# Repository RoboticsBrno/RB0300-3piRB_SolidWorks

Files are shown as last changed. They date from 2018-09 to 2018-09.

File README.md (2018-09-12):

# SOČ 2016 - Nadstavbová deska pro robota Pololu 3pi
**Autor:** Petr Bobčík

Vítejte v příloze mé práce Nadstavbová deska pro robota Pololu 3pi

#### V této příloze naleznete: 
1) Dokumenty
1) Eagle
1) Obhajoba
1) Použité obrázky
1) SolidWorks

#### Podrobnější obsah jednotlivých složek:
1) Přehled projektu s grafm pro IR senzor, obrázek s konceptem zapojení a tabulku potřebných součástek na pájení.
2) Finální verze desky a schéma k ní v programu Eagle + schéma s deskou k nárazovému senzoru.
3) Text samotné sočky a prezentaci k ní.
4) Veškeré obrázky použity jak v prezentaci, tak v textové práci.
5) Kompletní 3D model robota Pololu 3pi s přídavným shieldem.

## Cíl práce
<p>Cílem této práce byl návrh nadstavbové desky (shieldu) pro robota Pololu 3pi. Konstrukce robota je od výrobce optimalizována
na soutěžní disciplínu „sledování čáry“, kde robot dosahuje výborných výsledků a nemá mezi komerčně dostupnými produkty konkurenci. Ovšem při složitější variantě této disciplíny “najdi čáru“, konající se na Robotickém dni v Praze, kde dráha obsahuje rozpojky, odbočky, nebo překážky, není možné s ním závodit. Můj shield může posloužit, kromě možné účasti na soutěžích, také ve výuce. V ní si student může
robota sám naprogramovat. Přidáním funkcí a senzorů bude robot univerzálnější než doposud.</p>

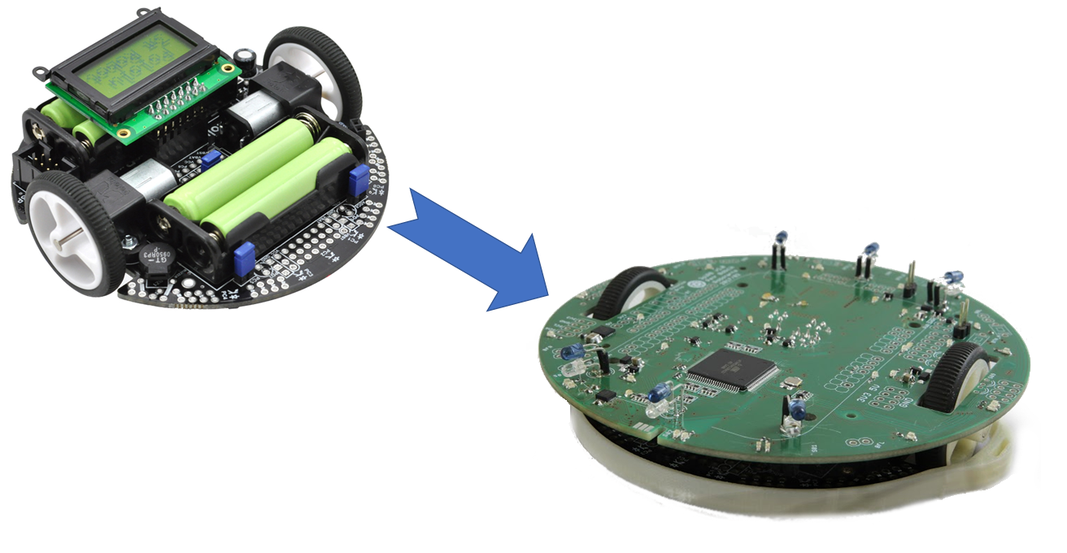
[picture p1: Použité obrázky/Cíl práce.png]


<p>Práce řeší rozšíření možností využití robota Pololu 3pi návrhem nadstavby s doplňkovými funkcemi.
Přidané funkce umožňují robotovi snímat podněty ze svého okolí. Další navrženou částí je nárazník pro ochranu před mechanickým poškozením, ke kterému v praxi velmi často dochází. Tyto nárazy způsobovli nefunkčnost senzorů odrazivosti nebo dokonce i jejich odlomení od desky.</p>

Můj přídavný shield je také pinově kompatibilní s bastlířskými deskami, jako je **Arduino Uno**, **FRDM-KL25Z**, **FRDM-KL46Z** a **FRDM-K64F**. Je tedy možné a plánované, že pro přidání dalších funkcí, které můj shield neobsahuje, je možné připevnit jednu ze zmíněných desek, nebo desku, která má shodný pinout. Mikrokontroler, ATmega328P, který je na základním modelu robota se využívá jako MCU pro motory a hlavní řídící mikrokontroler je AVR XMEGu A1, který se nachází na mém shieldu. Ten mi poskytuje velký počet pinů s potřebnými periferiemi. 

## Jaké funkce jsou prostřednictvím shieldu přidány?
<p>Tato práce přidává robotovi Pololu 3pi schopnost detekovat překážku pomocí IR senzorů, kterých je na shieldu celkem 8 po 45° nebo pomocí nárazového senzoru, upevněného na mnou navržený nárazník. Dále také k orientaci v prostoru je přidáno IMU (inerciální pohybová jednotka), která obsahuje gyroskop, magnetometr a akcelerometr v jednom pouzdře. Posledním senzorem je enkodér, pomocí kterého můžeme měřit ujetou vzdálenost, zajišťuje přesnější otáčení okolo osi a umožňuje také měřit rychlost.</p><p>Na desce je přidán také chip pro nabíjení baterií, takže není zapotřebí vytahovat tužkové baterie, které se na základní verzi robota nacházejí. Pouzdra s tužkovými bateriemi je tedy možné vytáhnout a tím snížit váhu. Shield také obsahuje obvod pro měření baterie a to jak napětí, tak proudu. Tímto měřením je možné hlídat úroveň nabití baterie nebo dokonce detekovat, zda baterie není poškozená.</p>

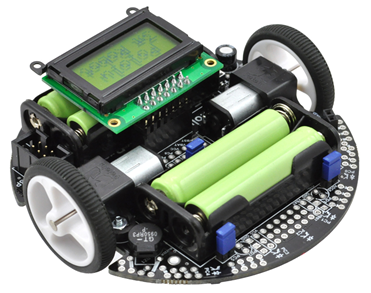
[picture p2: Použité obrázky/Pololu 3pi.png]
Robot Pololu 3pi
## Co je vlastě Pololu 3pi? 
<p>Je to velmi rychlý komerčně dostupný soutěžní robot, určený na disciplínu s názvem sledování čáry, která je v České republice velmi populární (tato disciplína je více popsaná níže). Jeho průměr je 95 mm (odtud dostal název 3pi) a hmotnost 83 g (bez baterií). Jeho rychlost se pohybuje okolo 1m/s. Hlavním mozkem celého robota je mikrokontrolér ATmega328P, který se nachází například u Arduino Nano. Tento robot je vhodný pro začínající programátory, kteří se chtějí od začátečních robotů, jako například legových ze stavebnice Mindstorm, posunout o kousek dále a chtějí se naučit programovací.</p>

## Sledování čáry
</p>Úkolem robota je, aby následoval černou čářu, která se pod ním nachází. Nejprve šlo jen o jízdu po čáře, ale v poslední době se zmíněná disciplína výrazně ztížila, přidáním rozdvojení, křižovatky, přerušení a překážky. Pololu 3pi nedokáže tyto nové prvky řešit, a proto jsem se rozhodl přidat potřebné funkce, které to zajistí.<p>

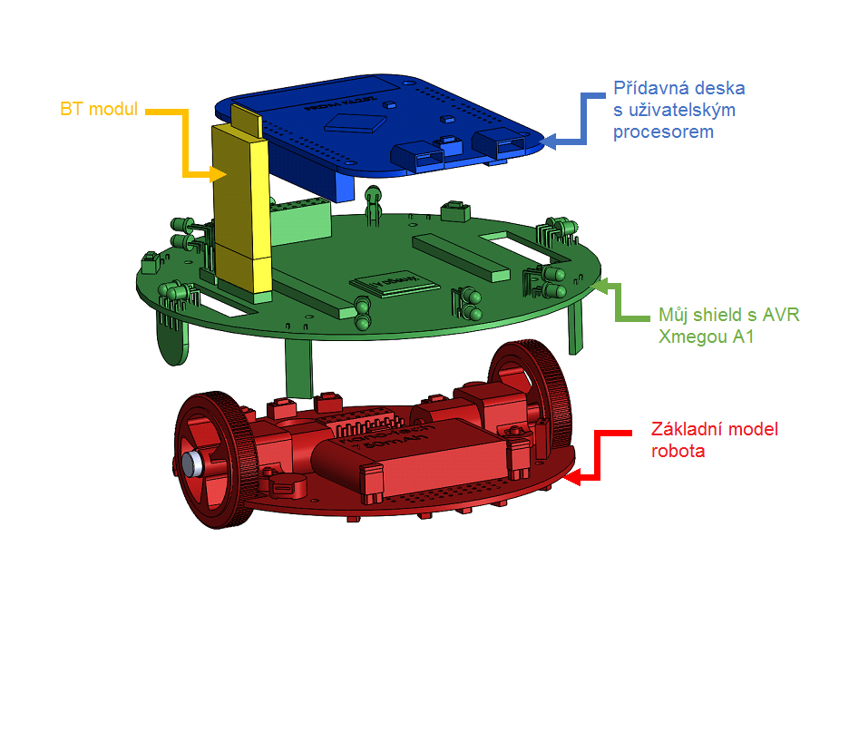
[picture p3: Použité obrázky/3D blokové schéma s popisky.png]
Pololu 3pi s mým shieldem

#### [Více informací naleznete na stránkách Robotárny k mojí SOČ](https://www.robotikabrno.cz/robotarna/projekty-a-socky/soc-2017-petr-bobcik-nadstavbova-deska-pro-robota-pololu-3pi). 

Tato práce byla vypracována společně s [Robotárnou](www.robotarna.cz) a [SPŠ a VOŠ Sokolská Brno](www.spssbrno.cz).

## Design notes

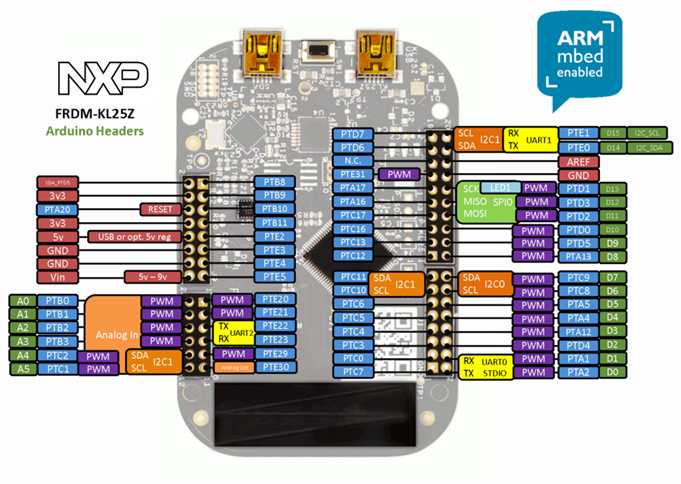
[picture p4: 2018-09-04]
Použité obrázky/FRDM KL25Z-pinout.png

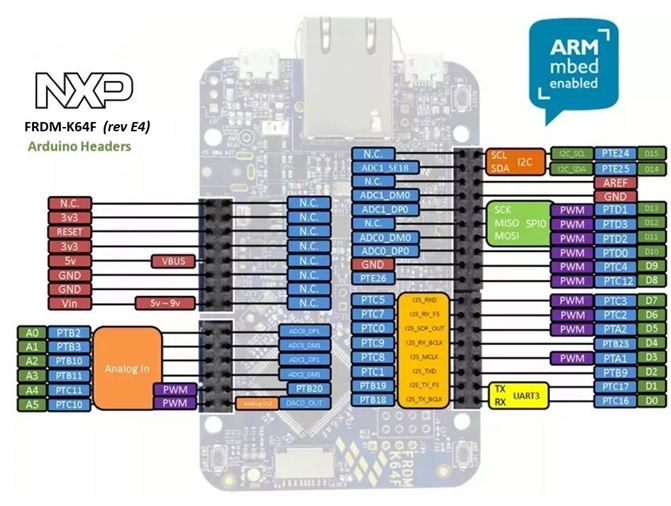
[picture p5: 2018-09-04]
Použité obrázky/FRDM K64F-pinout.png

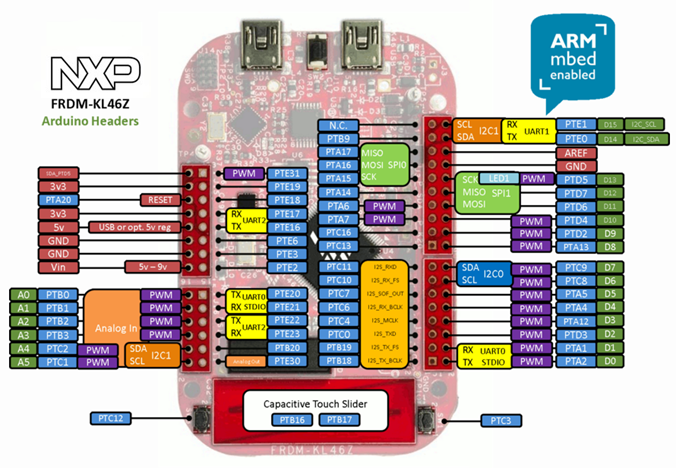
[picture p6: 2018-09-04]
Použité obrázky/FRDM KL46Z-pinout.png

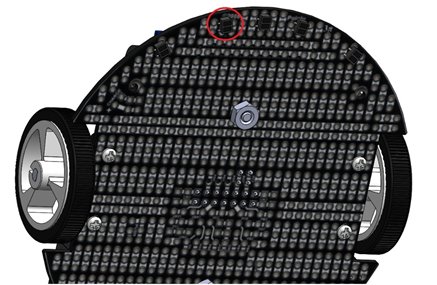
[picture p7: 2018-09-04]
Použité obrázky/Senzory odrazu.png

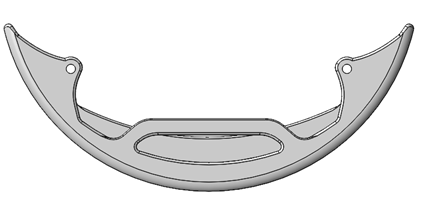
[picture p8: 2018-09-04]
Použité obrázky/Poloviční nárazník.png

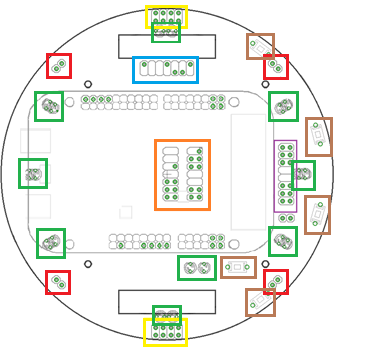
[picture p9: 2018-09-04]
Použité obrázky/Umístěné součástky, o kterých jsem věděl, kde budou.png

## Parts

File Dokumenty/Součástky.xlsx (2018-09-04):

Qty | Value | Device | Package | Parts | Description | MF | MPN | OC_FARNELL | OC_GME | OC_NEWARK | PACKAGE | PN | SUPPLIER
1 | 1X7 | PINHD-1X7 | BLUETOOTH_CONNECTOR_TOP | BLUETOOTH_CONNECTOR_TOP
1 |  | DIODE-0603 | D0603 | D1 | DIODE
1 | 1X7 | PINHD-1X7 | DISPLAY_INPUT | DISPLAY_INPUT
3 |  | L-USL0805 | R0805@1 | L4, L5, L8 | INDUCTOR, American symbol
5 |  | N-MOSFET-SOT323-GSD | SOT323 | Q3, Q4, Q7, Q8, Q14 |  |  |  | 2543537
1 | 1X1 | PINHD-1X1 | 1X01 | IMU_FSYNC | PIN HEADER
1 | 1X2 | PINHD-1X2 | 1X02 | PWR_PINS | PIN HEADER
1 | 1X4 | PINHD-1X4 | 1X04 | SENSOR_I2C | PIN HEADER
1 | 1X6 | PINHD-1X6 | 1X06 | JP2 | PIN HEADER
1 | 1X8 | PINHD-1X8 | 1X08 | JP4 | PIN HEADER
1 | 2X2 | PINHD-2X2 | 2X02 | PWR-SHDN | PIN HEADER
4 | 2X4 | PINHD-2X4 | 2X04 | ENCODER_LEFT, ENCODER_RIGHT, LDC_I2C1, SUPPLY_CONNECTOR_5V-3V3 | PIN HEADER
1 | 2X7 | PINHD-2X7 | 2X07 | JP7 | PIN HEADER
1 |  | R-EU_R0603 | R0603 | FERITE_BEAD | RESISTOR, European symbol
19 | 100k | RESISTOR_0402MP | _0402MP | R3, R9, R11, R18, R19, R29, R43, R48, R77, R92, R94, R117, R132, R133, R141, R152, R159, R160, R166 | Resistors |  |  | 2502498
2 | 100n | C-EUC0402 | C0402 | C49, C50 | CAPACITOR, European symbol
34 | 100n/16V | C-EUC0402 | C0402 | C2, C3, C4, C8, C17, C18, C20, C21, C22, C23, C25, C29, C30, C31, C32, C33, C34, C35, C36, C37, C40, C41, C45, C46, C53, C56, C57, C58, C59, C61, C62, C63, C64, C65 | CAPACITOR, European symbol
29 | 10k | RESISTOR_0402MP | _0402MP | R1, R2, R24, R25, R26, R27, R28, R30, R31, R33, R34, R35, R39, R46, R50, R51, R71, R72, R73, R74, R75, R87, R98, R135, R148, R162, R167, R169, R170 | Resistors |  |  | 1469669 (http://cz.farnell.com/vishay/crcw040210k0fked/res-thick-film-10k-1-0-063w-0402/dp/1469669)
5 | 10n/16V | C-EUC0402 | C0402 | C5, C15, C42, C51, C52 | CAPACITOR, European symbol |  |  | 1758924RL (http://cz.farnell.com/multicomp/mc0402b103k250ct/cap-mlcc-x7r-10nf-25v-0402/dp/1758924RL)
1 | 10n/16V | C-EUC0402K | C0402K | C48 | CAPACITOR, European symbol |  |  | 1758924RL (http://cz.farnell.com/multicomp/mc0402b103k250ct/cap-mlcc-x7r-10nf-25v-0402/dp/1758924RL)
3 | 10p/16V | C-EUC0603 | C0603 | C10, C24, C28 | CAPACITOR, European symbol |  |  | 1759102
15 | 10u/16V | C-EUC0805 | C0805 | C1, C6, C7, C9, C14, C19, C26, C27, C38, C39, C43, C44, C47, C55, C60 | CAPACITOR, European symbol |  |  | 1759246RL
2 | 10uH | L-EUSMD0603 | R0603 | L1, L3 | INDUCTOR, European symbol |  |  | 1463501
8 | 150R | RESISTOR_0402MP | _0402MP | R100, R118, R120, R122, R124, R126, R128, R130 | Resistors |  |  | 9239138 (http://cz.farnell.com/yageo-phycomp/rc0402fr-07150rl/res-thick-film-150r-1-0-063w-0402/dp/9239138)
1 | 16 MHz | ABM8 | ABM8 | Q2 |  |  |  | 2471850
6 | 220R | 742-8_MULTI | 742-8 | RN1, RN3, RN4, RN5, RN6, RN7 |  |  |  | 2060094
29 | 180R | RESISTOR_0402MP | _0402MP | R6, R8, R10, R12, R13, R20, R40, R41, R45, R54, R55, R56, R58, R59, R61, R62, R70, R78, R79, R108, R119, R121, R123, R125, R127, R129, R131, R138, R140 | Resistors |  |  | 2502516
7 | 220R | 742-8_MULTI | 742-8 | RN2, RN9, RN10, RN11, RN12, RN13, RN14 |  |  |  | 2060094
5 | 1M | RESISTOR_0402MP | _0402MP | R23, R32, R151, R163, R165 | Resistors |  |  | 1469667
2 | 1R | RESISTOR_0402MP | _0402MP | R156, R157 | Resistors |  |  | 2502492
1 | 1k | R-EU_R0402 | R0402 | R158 | RESISTOR, European symbol |  |  | 1469662
10 | 1k | RESISTOR_0402MP | _0402MP | R76, R88, R139, R142, R143, R144, R145, R146, R147, R154 | Resistors |  |  | 1469662
1 | 1m | RESISTOR1206 | 1206 | R155 | Resistors |  |  | 9241124
2 | 1u/16V | C-EUC0805 | C0805 | C16, C54 | CAPACITOR, European symbol |  |  | 2320832 (http://cz.farnell.com/multicomp/mc0805x105k250ct/cap-mlcc-x5r-1uf-25v-0805/dp/2320832)
1 | 1uH | XAL7030 | XAL7030 | L14 |  |  |  | 2289107
5 | 22k | RESISTOR_0402MP | _0402MP | R36, R38, R49, R136, R161 | Resistors |  |  | 2502529 |  |  |  | XAL7030-102MEC
3 | 22u/16V | C-EUC0805 | C0805 | C11, C12, C13 | CAPACITOR, European symbol |  |  | 2611932
1 | 2k | RESISTOR_0402MP | _0402MP | R60 | Resistors |  |  | 2502522
1 | 330R | RESISTOR_0402MP | _0402MP | R37 | Resistors |  |  | 2502541
1 | 330k | RESISTOR_0402MP | _0402MP | R21 | Resistors |  |  | 2324303
1 | 2X7 | PINHD-2X7 | 3PI_BT_CONNECTOR | 3PI_CONNECTOR
2 | 44,2k | RESISTOR_0402MP | _0402MP | R22, R99 | Resistors |  |  | 2668223
1 | AVR_XMEGA_A1_100A | AVR_XMEGA_A1_100A | TQFP100 | IC4 | Device for Atmel AVR XMEGA A1 Series |  |  | 1715520
1 | BATTERY_LI-POL | PINHD-1X2 | 1X02 | BAT_CONNECTOR | PIN HEADER
1 | BT_COM_VOLTAGE_SETTING | PINHD-1X3 | 1X03 | JP1 | PIN HEADER
4 | BUMPER_COIL | PINHD-1X2 | 1X02 | SENSOR_BACK_LEFT, SENSOR_BACK_RIGHT, SENSOR_FRONT_LEFT, SENSOR_FRONT_RIGHT | PIN HEADER
1 | CON_PROG-6SMD | CON_PROG-6SMD | SMD-6 | JP3
4 | DB2X41500L | SHOTTKY-SOD123 | SOD123 | D2, D5, D6, D7 |  |  |  | 2284963
3 | FDMC510P | P-MOSFET-MLP_HS | MLP3.3X3.3_HS | Q1, Q13, Q17 |  |  |  | 1885764
1 | FRDM-KL25Z+KL46Z+K64F_MORE_PINS | FRDM-KL25Z+KL46Z+K64F_MORE_PINS | FRDM-KL25Z+KL46Z+K64F_MORE_PINS | U$1
1 | INA210AIDCKT | INA213AIDCKT | SOT65P210X110-6N | U1 | BIDIRECTIONAL CURRENT SHUNT MONITOR |  | INA210AIDCKT | 1754837
9 | L-934F3C | LED3MM | LED3MM | LED6, LED7, LED8, LED9, LED20, LED21, LED22, LED23, LED24 | LED |  |  | 2290438 | 511-503 |  | SC-70-6 |  | Texas Instruments
9 | L-93DP3BT | LED3MM | LED3MM | FOTOTR_3MM_01, FOTOTR_3MM_02, FOTOTR_3MM_03, FOTOTR_3MM_04, FOTOTR_3MM_05, FOTOTR_3MM_06, FOTOTR_3MM_07, FOTOTR_3MM_08, FOTOTR_3MM_09 | LED |  |  | 2290440 | 520-068
1 | LDC1614-WQFN | LDC1614-WQFN | LDC1614-WQFN | U$3 |  |  |  | 2465057 (http://cz.farnell.com/texas-instruments/ldc1614rght/ldc-28bit-4-ch-2-7-3-6v-wqfn-16/dp/2465057)
4 | M74VHC1GT125DF2G | 741G125 | SOT353 | IC1, IC2, IC3, IC5 |  |  |  | 2534357RL
1 | MCP73831T-2ATI/OT | MCP73831T-2ATI/OT |  | IC13 | IC, BATT CHARGER, Li-Ion Li-Polymer, 500 mA |  | MCP73831T-2ATI/OT | 1834890
1 | MPU-9250 | MPU-9250 | LEAD-QFN24 | U$4 |  |  |  | 1834890 |  | 84R5196 | SOT23-5 |  | Microchip
5 | NTJD5121NT1G | NTJD5121NT1G | SOT363 | Q5, Q6, Q9, Q10, Q18 | NTJD5121N, Dual N-Channel with ESD | ON SEMICONDUCTOR | NTJD5121NT1G | 2317611
1 | 2X8 | PINHD-2X8 | PINHEAD_2X8_DISPLAY | DISPLAY_OUTPUT_BACKLIGHT |  |  |  |  |  | unknown
5 | TACTM-35N-F | TACTM-35N-F | TACTM-35N-F | BTN_LEFT, BTN_MIDDLE, BTN_OPTION, BTN_PWR, BTN_RIGHT |  |  |  | Objednáno odjinud
1 | TPS61236 | TPS61236 | VQFN | U5_STEP-UP |  |  |  | 2507105
1 | TPS73025DBV | TPS73033DBV | SOT23-DBV | IC7_XMEGA_AREF |  |  |  | 1135395 |  |  |  | TPS61236
1 | TPS73033DBV | TPS73033DBV | SOT23-DBV | IC6_XMEGA_3V3 |  |  |  | 1135395
1 | USB-MICRO-B-BOTTOM | USB-MICRO-B-BOTTOM | USB-MICRO-B-BOTTOM-MOLEX | X3
17 | green | LEDCHIPLED_0603 | CHIPLED_0603 | LED2, LED4, LED10, LED12, LED14, LED16, LED18, LED25, LED26, LED30, LED32, LED34, LED35, LED36, LED37, LED38, LED39 | LED |  |  | 1850749
9 | red | LEDCHIPLED_0603 | CHIPLED_0603 | LED1, LED3, LED5, LED11, LED13, LED15, LED17, LED19, LED27 | LED

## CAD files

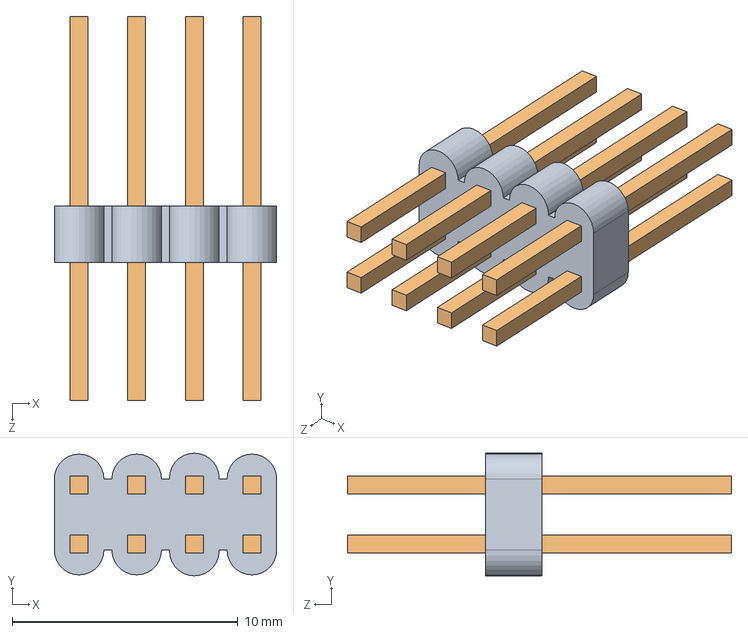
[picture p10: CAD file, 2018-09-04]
SolidWorks/PINHEAD_ENKODER.SLDASM
9.85 x 5.43 x 17.0 mm
NASADA_NA_PINY-ENKODER
PIN x 8

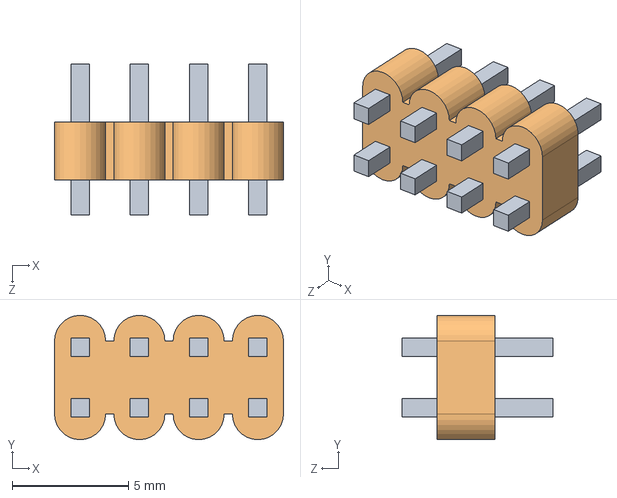
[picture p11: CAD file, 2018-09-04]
SolidWorks/PINHEAD_ENKODER_K_DESCE.SLDASM
9.85 x 5.35 x 6.50 mm
PIN x 8
NASADA_NA_-ENKODER

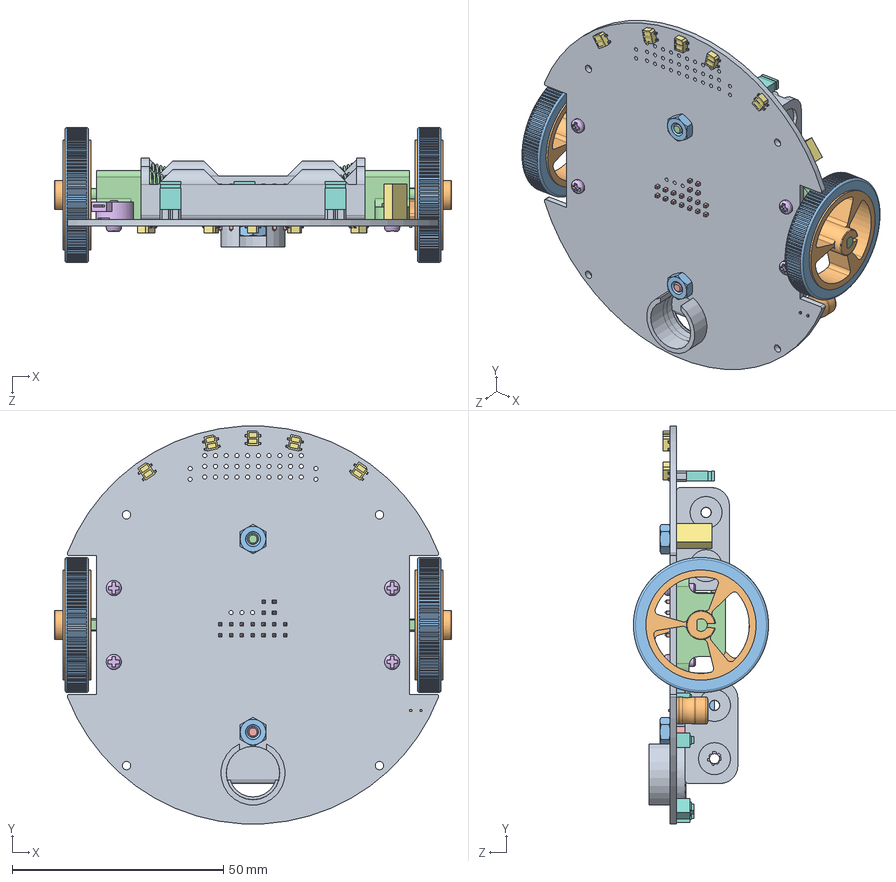
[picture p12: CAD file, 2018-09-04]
SolidWorks/pololu_3pi_model/_POLOLU_3PI.SLDASM
94.0 x 94.1 x 32.0 mm
DESKA
KOLO x 2
PNEUMATIKA x 2
MOTOR x 2
MATICKA x 4
SROUB x 4
SENSOR x 5
TLACITKO x 5
POUZDRO_NA_BATERKI x 2
KONDENZATOR
BEDNA
PRUZINA x 4
KRATSI_PIN x 18
REPRAK
DUTINKA
KRYTKA_PINU x 3
DODATEK K POUZDRU x 3
NASADA_NA_PINY_2x2
MATICKA_K_BATERKAM x 2
SROUB_K_BATERKAM
SROUB_K_BATERKAM – 2
SPUNT_KE_KRYTCE_K_BATERKAM x 4

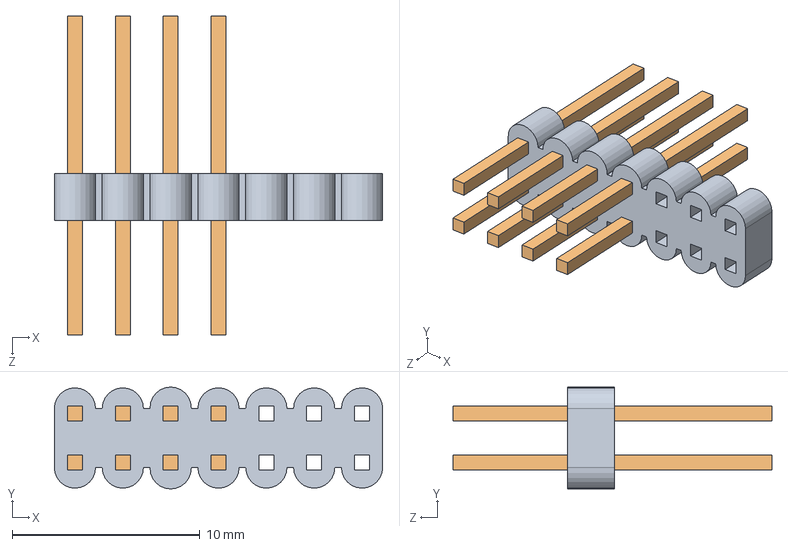
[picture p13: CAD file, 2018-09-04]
SolidWorks/PINHEADY_3PI.SLDASM
17.5 x 5.43 x 17.0 mm
NASADA_NA_PINY-ENKODER
PIN x 8

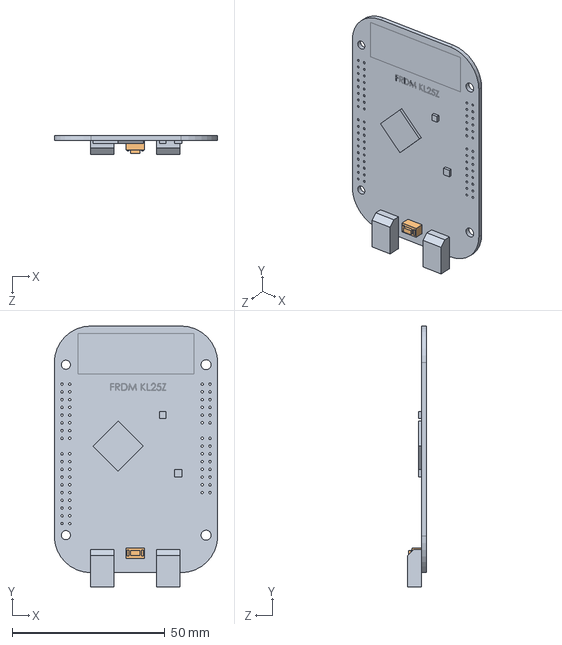
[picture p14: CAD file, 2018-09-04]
SolidWorks/FRDM_KOMPLET.SLDASM
53.6 x 85.6 x 6.09 mm
FRDM-KL25Z
TLACITKO

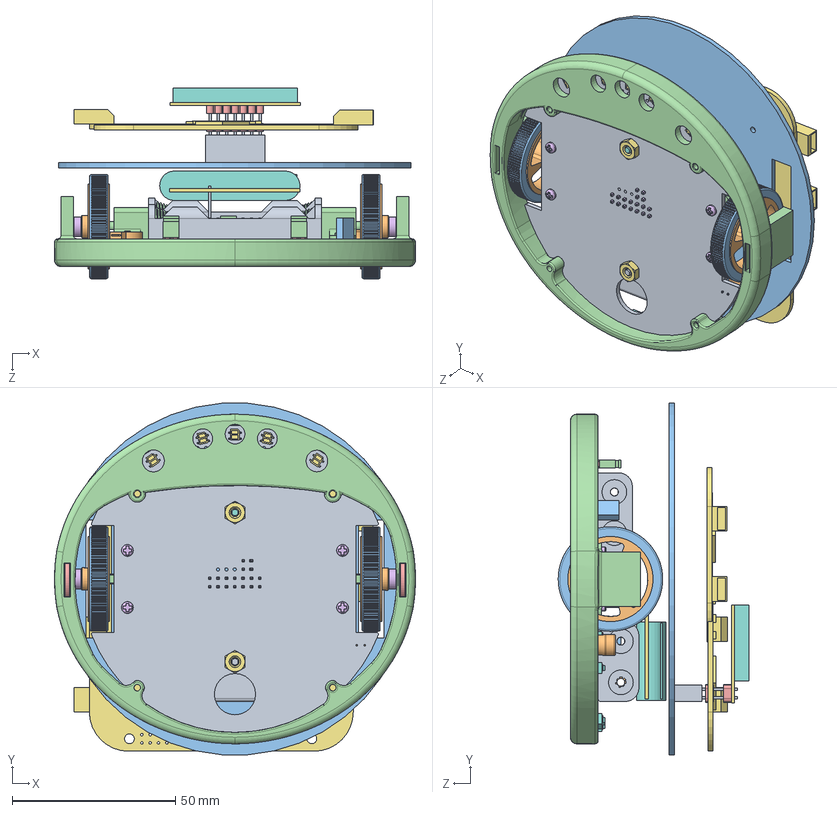
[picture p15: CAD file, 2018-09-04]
SolidWorks/3PI_S_NARAZNIKEM.SLDASM
110.6 x 107.7 x 58.4 mm
DESKA
KOLO x 2
PNEUMATIKA x 2
MOTOR x 2
MATICKA x 4
SROUB x 4
SENSOR x 5
TLACITKO x 5
POUZDRO_NA_BATERKI x 2
KONDENZATOR
BEDNA
PRUZINA x 4
NASADA_NA_PINY-ENKODER x 3
KRATSI_PIN x 18
REPRAK
DUTINKA
KRYTKA_PINU x 3
DODATEK K POUZDRU x 3
NASADA_NA_PINY_2x2
MATICKA_K_BATERKAM x 2
SROUB_K_BATERKAM
SROUB_K_BATERKAM – 2
SPUNT_KE_KRYTCE_K_BATERKAM x 4
HORNI_DESKA
NARAZNIK_NA_ROCNIKOVKU
CHIP x 2
magnet x 2
FRDM-KL25Z x 2
Li-pol_baterie_750mAh
PIN x 14
DESKA POD DISPLAY
DISPLAY
HLAVA

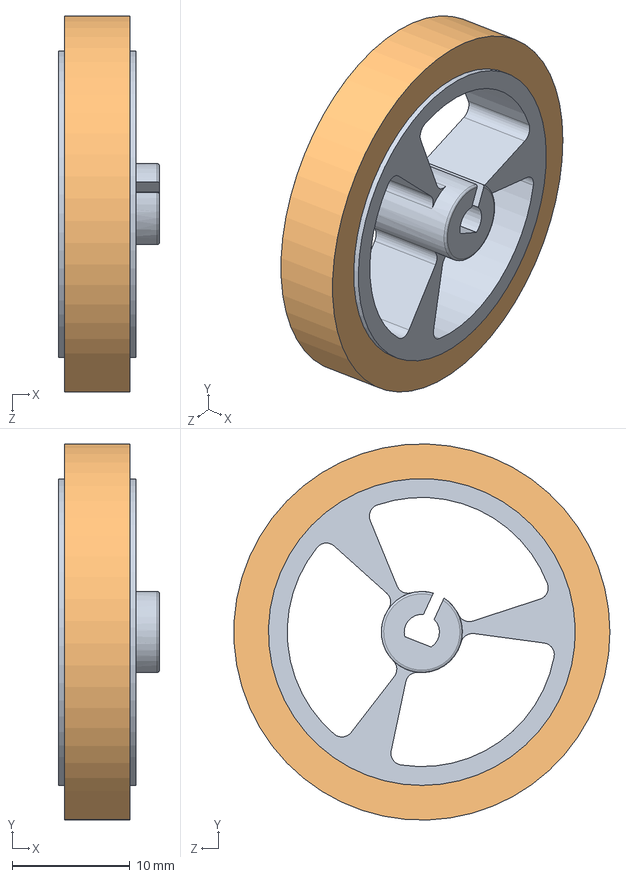
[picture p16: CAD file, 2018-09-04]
SolidWorks/pololu_3pi_model/KOLO1.SLDASM
8.60 x 32.0 x 32.0 mm
KOLO
PNEUMATIKA

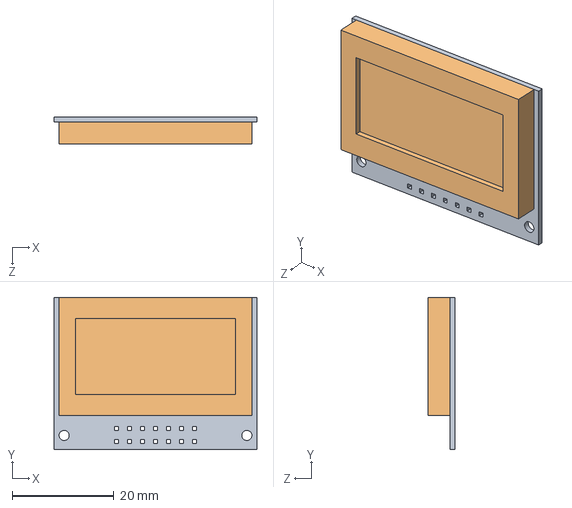
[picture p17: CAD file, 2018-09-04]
SolidWorks/pololu_3pi_model/DISPLAY_ROCNIKOVKA.SLDASM
40.0 x 30.0 x 5.30 mm
DESKA POD DISPLAY
DISPLAY

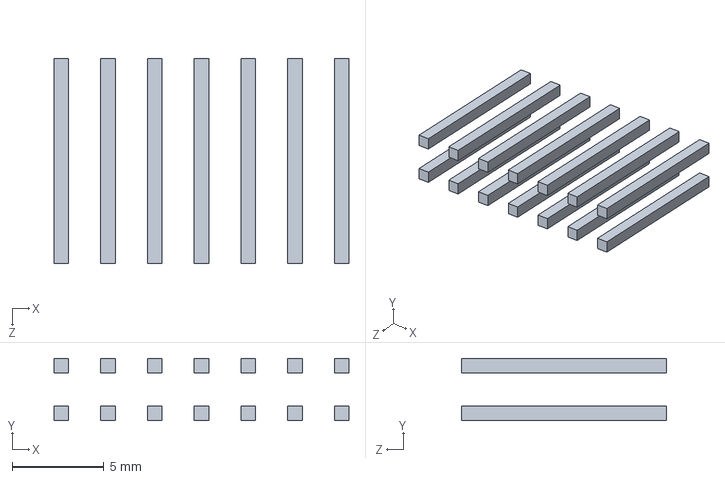
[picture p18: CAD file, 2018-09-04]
SolidWorks/pololu_3pi_model/PINHEAD_KRATSI.SLDASM
16.1 x 3.40 x 11.2 mm
KRATSI_PIN x 14

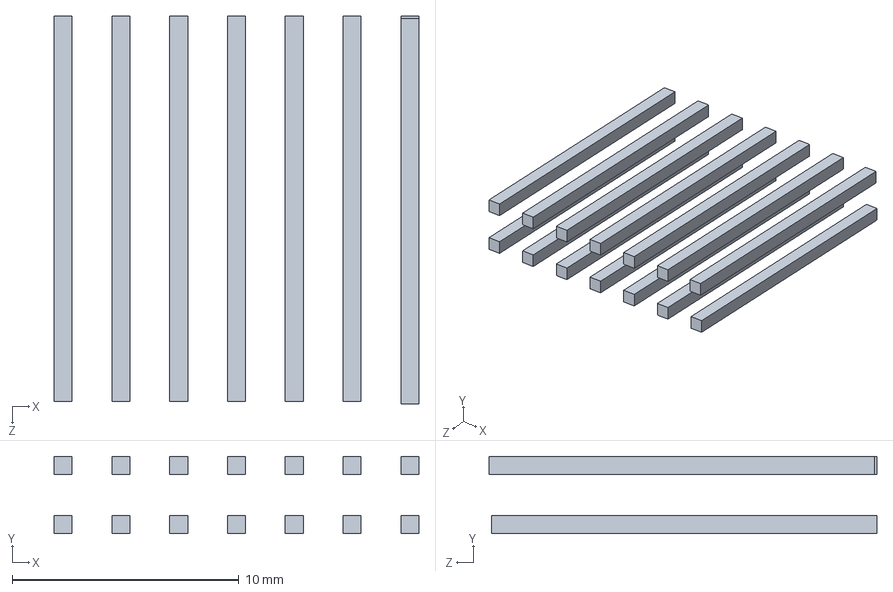
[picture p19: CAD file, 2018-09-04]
SolidWorks/pololu_3pi_model/PINHEDY.SLDASM
16.1 x 3.40 x 17.1 mm
PIN x 14

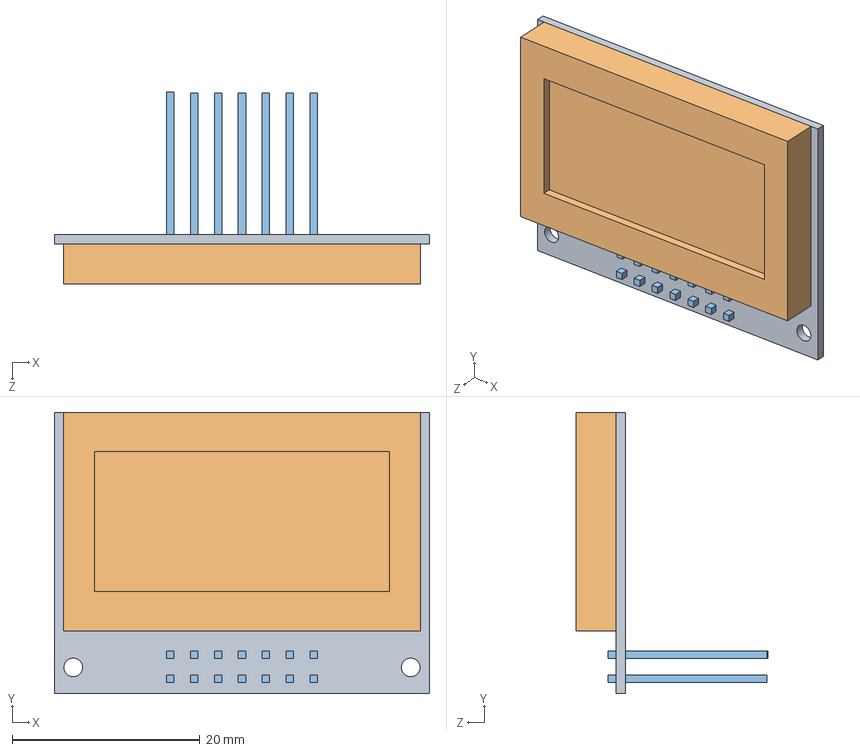
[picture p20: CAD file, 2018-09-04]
SolidWorks/pololu_3pi_model/DISPLAY.SLDASM
40.0 x 30.0 x 20.5 mm
DESKA POD DISPLAY
DISPLAY
PIN x 14

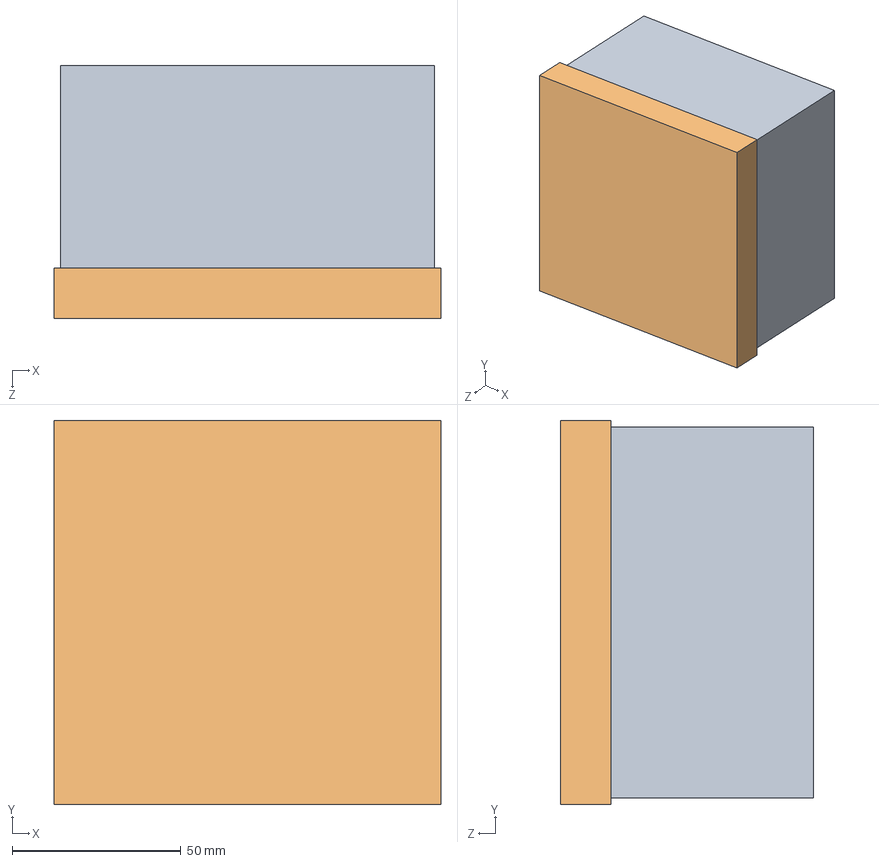
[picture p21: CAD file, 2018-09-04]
SolidWorks/pololu_3pi_model/KRABICKA_NA_3PI.SLDASM
114.8 x 114.1 x 75.1 mm
KRABICKA_NA_3PI
DEKL_KE_KRABICCE_NA_3PI
DESKA
KULICKA
KOLO x 2
PNEUMATIKA x 2
MOTOR x 2
MATICKA x 12
SROUB x 4
SENSOR x 5
TLACITKO x 5
POUZDRO_NA_BATERKI x 2
HLAVA
KONDENZATOR
BEDNA
PRUZINA x 4
NASADA_NA_PINY x 3
KRATSI_PIN x 18
DESKA POD DISPLAY
DISPLAY
PIN x 14
CHRÁNIČ
VRCHNI_DESKA
REPRAK
DUTINKA
TYCKA_V_PREDU x 2
TYCKA_V_ZADU x 2
KRYTKA_PINU x 3
DODATEK K POUZDRU x 3
NASADA_NA_PINY_2x2
MATICKA_K_BATERKAM x 2
SROUB_K_BATERKAM
SROUB_K_BATERKAM – 2
BATERIE x 4
SPUNT_KE_KRYTCE_K_BATERKAM x 4

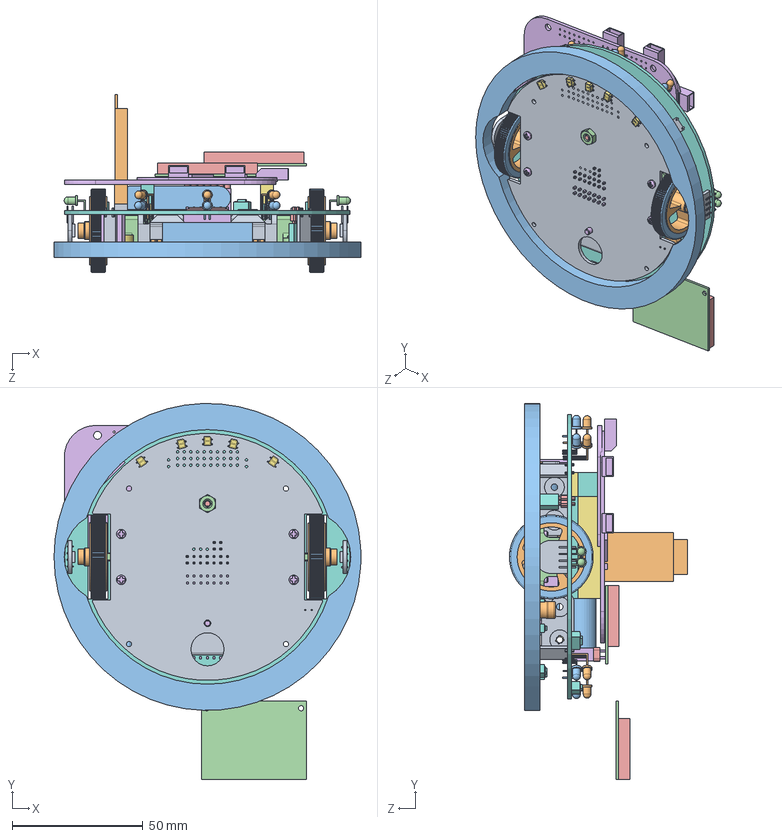
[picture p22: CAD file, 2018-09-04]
SolidWorks/_Pololu_3pi_SOČ.SLDASM
117.2 x 143.6 x 68.0 mm
DESKA
KOLO x 2
PNEUMATIKA x 2
MOTOR x 2
MATICKA x 4
SROUB x 4
SENSOR x 5
TLACITKO x 9
KONDENZATOR
BEDNA
NASADA_NA_PINY_U_MOTORU x 3
KRATSI_PIN x 46
REPRAK
DUTINKA
KRYTKA_PINU x 3
DODATEK K POUZDRU x 3
NASADA_NA_PINY_2x2
HORNI_DESKA
CHIP x 2
magnet x 2
FRDM-KL25Z x 2
Li-pol_baterie_750mAh
DUTINKA_KRATSI
DUTINKA_DELSI
NARAZOVY_SENZOR x 4
IR_SENZOR_PRIJIMAC x 6
IR_SENZOR_VYSILAC x 6
IR_SENZOR_PRIJIMAC_KRATKY x 4
XMEGA_A1
DUTINKA_K_BLUETOOTH x 3
PINHEAD_POD_FRDM_DELSI
PINHEAD_POD_FRDM_KRATSI
3PI_BT_CONNECTOR
MOLITANOVY_NARAZNIK
PINHEAD_5V_3V3
PINHEAD_1x2
DESKA POD DISPLAY
DISPLAY
Deska ke kamere

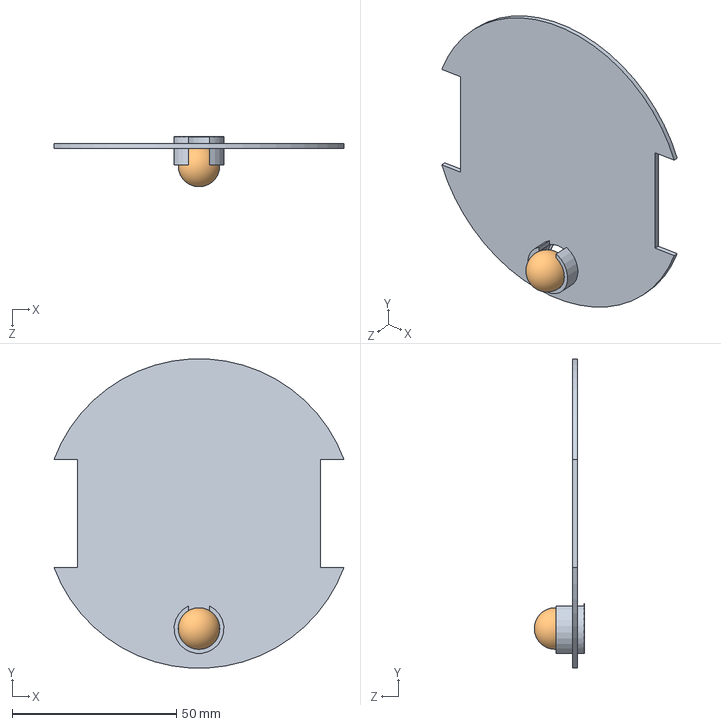
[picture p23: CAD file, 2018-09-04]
SolidWorks/pololu_3pi_model/DESKA+KULICKA.SLDASM
88.3 x 94.1 x 15.4 mm
DESKA
KULICKA

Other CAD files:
SolidWorks/FRDM-KL25Z.SLDASM
SolidWorks/pololu_3pi_model/MOTOR+KOLO.SLDASM
SolidWorks/IR_SENZOR_KOMPLET.SLDASM
SolidWorks/pololu_3pi_model/POUZDRO_NA_BATERKY.SLDASM
SolidWorks/3PI_BT_CONNECTOR.SLDPRT
SolidWorks/BLUETOOTH_MODUL.SLDPRT
SolidWorks/CHIP.SLDPRT
SolidWorks/DUTINKA_DELSI.SLDPRT
SolidWorks/DUTINKA_KRATSI.SLDPRT
SolidWorks/Deska ke kamere.SLDPRT
SolidWorks/FRDM-KL25Z.SLDPRT
SolidWorks/HORNI_DESKA.SLDPRT
SolidWorks/IR_SENZOR.SLDPRT
SolidWorks/IR_SENZOR_PRIJIMAC.SLDPRT
SolidWorks/IR_SENZOR_PRIJIMAC_KRATKY.SLDPRT
SolidWorks/IR_SENZOR_VYSILAC.SLDPRT
SolidWorks/KARTACEK.SLDPRT
SolidWorks/KRYT_SROUBU_NA_DISTANCNI_SLOUPKY.SLDPRT
SolidWorks/Li-pol_baterie_5000mAh.SLDPRT
SolidWorks/Li-pol_baterie_750mAh.SLDPRT
SolidWorks/MOLITANOVY_NARAZNIK.SLDPRT
SolidWorks/NARAZNIK.SLDPRT
SolidWorks/NARAZNIK_NA_ROCNIKOVKU.SLDPRT
SolidWorks/NARAZNIK_NA_ROCNIKOVKU_DIL_A.SLDPRT
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

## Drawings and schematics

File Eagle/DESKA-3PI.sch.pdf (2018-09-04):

# GND

100n/16V

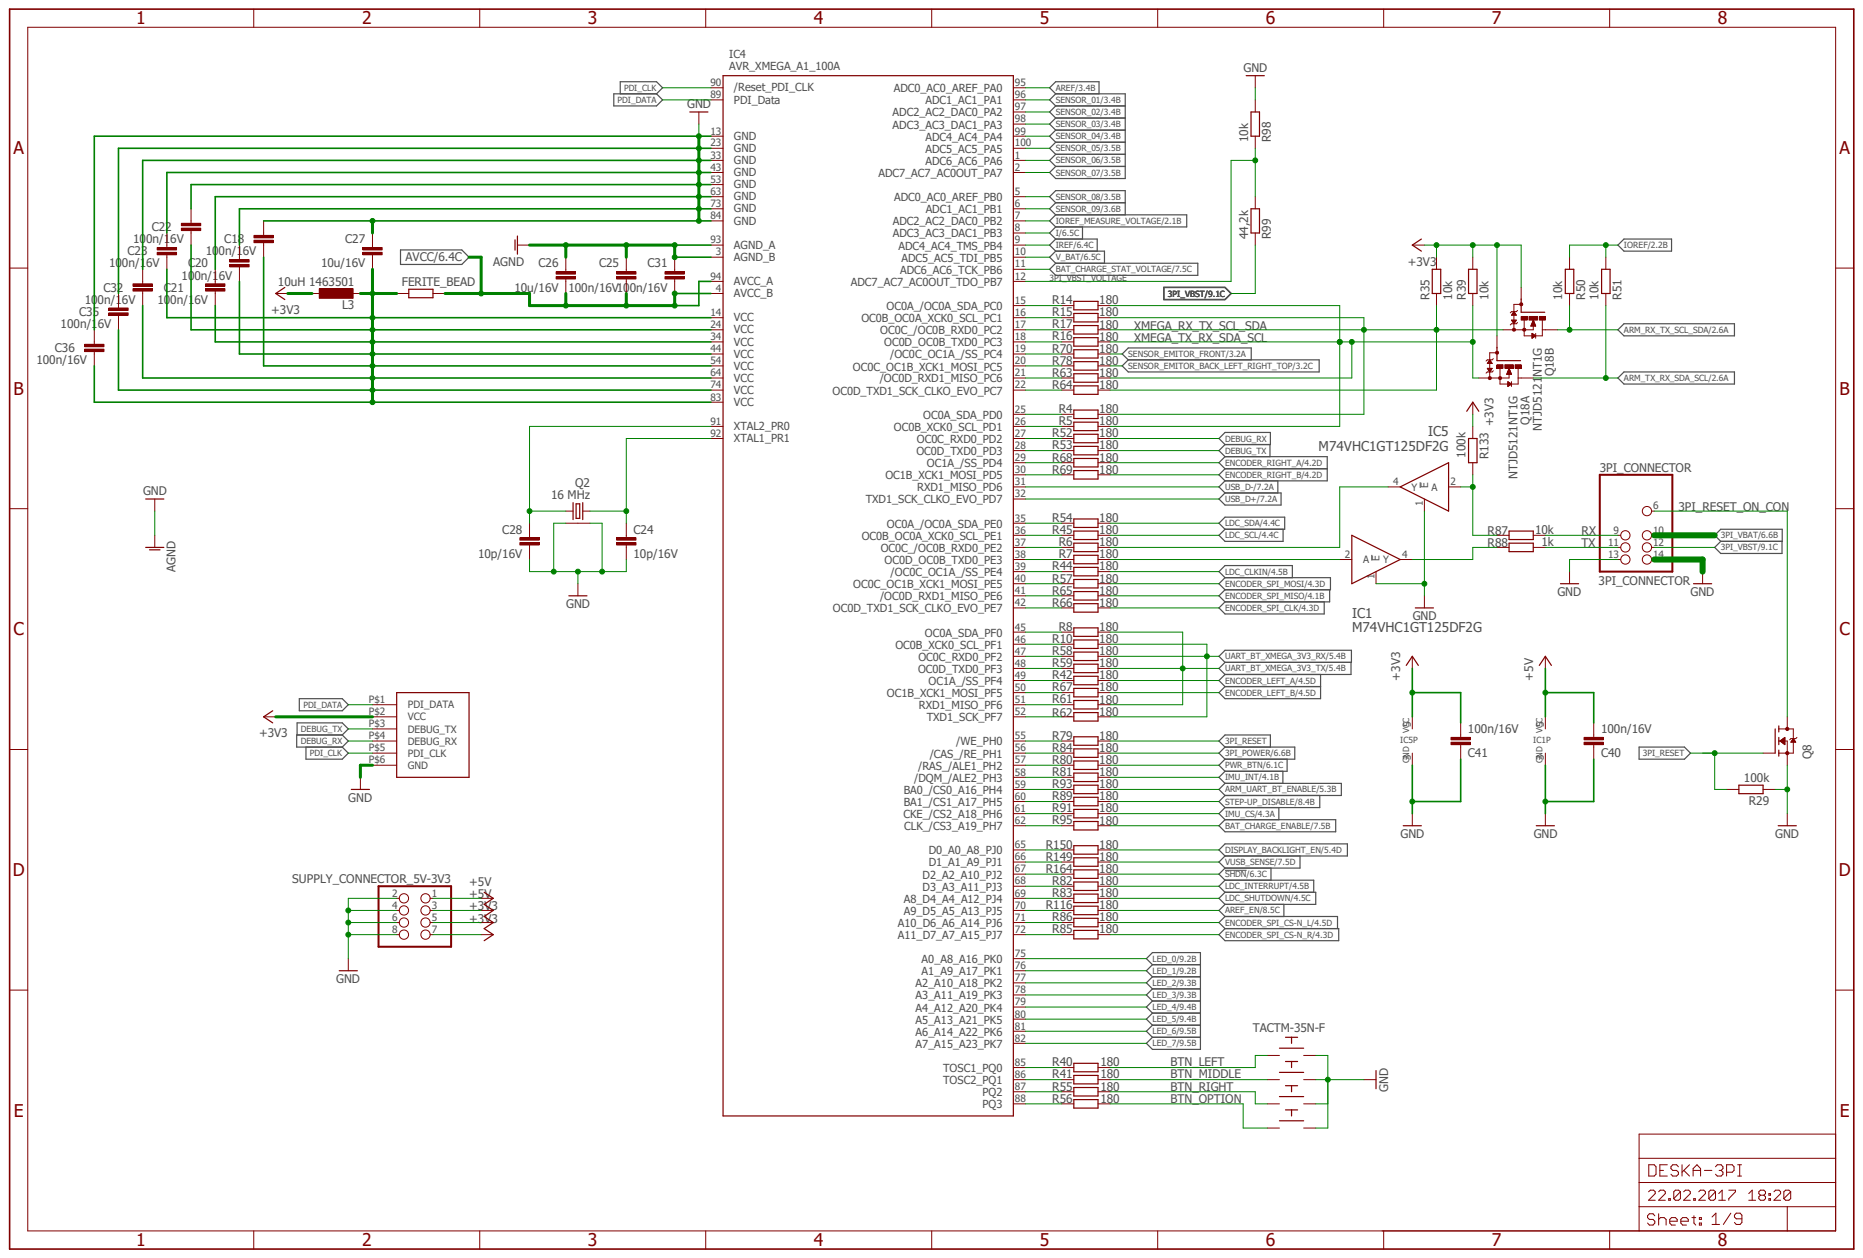
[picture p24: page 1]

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
34 | | R16 180
44
54
74 | R64 180
83 | R4 180

VCC GND

# PRI ZAPOJENI S ARDUINEM BUDE NAPAJENI PROCHAZET

# PRES P5V_USB (J3_10) A V PRIPADE FRDM DESKY

# PUJDE PRES P5-9V_VIN

(J3_16)

# (6-8) mA - signal traces (12) dA - low power traces (24) dA - middle power traces (32) A - high power traces (70) 10A - power suplly traces

# width [mil] current description

Definition for FRDM KL25Z Definition for FRDM KL46Z Definition for FRDM K64F | GND GND

+5V

180
180

10k

22k

# GND

R12
R13

R46

R49

NC
NC
NC
NC | NC NC

NC

J1-1 | J1_1 J1-2 | J1_2 J1-3 | J1_3 J1-4 | J1_4
J4-12 J4_12 | J4-11 J4_11 | J4-10 J4_10 | J4-9 J4_9
J2-14 | J2_14
J2-16 | J2_16
J2-18 | J2_18
J2-20 | J2_20

# J3-16 J3_16

# J3-14 J3_14

# J3-12 J3_12

# J3-10 J3_10

# J3-4 J3_4

U$5

# UART_BT_ARM_IOREF_RX/5.2B

# UART_BT_ARM_IOREF_TX/5.2B

IOREF/1.8A IOREF_MEASURE_VOLTAGE/1.5A | ARM_RX_TX_SCL_SDA/1.8B

# ARM_TX_RX_SDA_SCL/1.8B

# DESKA-3PI

22.02.2017 18:20

# Sheet: 2/9

A

B

C

D

1 | 2 | 3 | 4 | 5 | 6

A

B

C

D

1 | 2 | 3 | 4 | 5 | 6
TPM1_CH0 | I2S0_TXD0
USB_CLKIN | TPM0_CH2 | I2S0_TX_BCLK
UART3_RX | ENET0_1588_TMR0 | FB_CS5 | FB_TSIZ1 | FB_BE23_16_BLS15_8
TSI0_CH2 | UART0_RX | TPM2_CH0
CAN0_TX | FTM2_CH0 | I2S0_TX_BCLK | FB_AD15 | FTM2_QD_PHA
LCD_P14 | TSI0_CH11 | TPM2_CH0 | I2S0_TX_BCLK
CAN0_RX | FTM2_CH1 | I2S0_TX_FS | FB_OE | TM2_QD_PHB
| LCD_P15 | TSI0_CH12 | TPM2_CH1 | I2S0_TX_FS
UART3_TX | ENET0_1588_TMR1 | FB_CS4 | FB_TSIZ0 | FB_BE31_24_BLS7_0
TSI0_CH3 UART0_TX | TPM2_CH1
LLWU_P6 | ADC0_SE15 | SPI0_PCS3 | UART1_RTS | FTM0_CH0 | FB_AD13 | I2S0_TXD0
LCD_P20 | ADC0_SE14 | TSI0_CH13 | EXTRG_IN | AUDIOUSB_SOF_OUT | CMP0_OUT | I2S0_TXD0
SPI1_PCS1 | UART3_CTS | FB_AD20
LCD_P43 | SPI0_MISO | UART2_TX | TPM0_CH3 | SPI0_MOSI
ADC1_SE4B | CMP0_IN2 | FTM3_CH4 | I2S0_MCLK | FB_AD7
LLWU_P8 | LCD_P24 | SPI0_PCS0 | UART1_TX | TPM0_CH3 | I2S0_MCLK
JTAG_TDI | EZP_DI | UART0_RX | FTM0_CH6
| | ADC1_SE5B | CMP0_IN3 | FTM3_CH5 | I2S0_RX_BCLK | FB_AD6 | FTM2_FLT0
LLWU_P10 | LCD_P26 | CMP0_IN0 | SPI0_MOSI | EXTRG_IN | I2S0_RX_BCLK | SPI0_MISO | I2S0_MCLK
| | | | | SPI2_SIN | SPI0_PCS5 | FB_AD28
NMI | TSI0_CH5 | I2C1_SDA | TPM0_CH1
ADC0_SE14 | SPI0_PCS4 | PDB0_EXTRG | USB_SOF_OUT | FB_AD14 | I2S0_TXD1
LCD_P27 | CMP0_IN1 | SPI0_MISO | AUDIOUSB_SOF_OUT | I2S0_RX_FS | SPI0_MOSI
JTAG_TDO | TRACE_SWO | EZP_DO | UART0_TX | FTM0_CH7
CMP0_IN1 | SPI0_SIN | USB_SOF_OUT | I2S0_RX_FS | FB_AD8
LCD_P30 | I2C1_SCL | I2S0_RX_FS
ADC0_SE4B | CMP1_IN0 | SPI0_PCS2 | UART1_CTS | FTM0_CH1 | FB_AD12 | I2S0_TX_FS
| | LCD_P28 | CMP0_IN2 | I2C0_SCL | TPM0_CH4 | I2S0_MCLK
LLWU_P9 | SPI0_SCK | LPTMR0_ALT2 | I2S0_RXD0 | FB_AD10 | CMP0_OUT | FTM0_CH2
| | | | LCD_P31 | I2C1_SDA | I2S0_RXD0
| | | | | UART4_CTS | FB_AD26
LCD_P29 | CMP0_IN3 | I2C0_SDA | TPM0_CH5 | I2S0_RX_BCLK
CLKOUT32K | ENET_1588_CLKIN | UART4_CTS | RTC_CLKOUT | USB_CLKIN
| | | LCD_P33 | TPM_CLKIN1
JTAG_TCLK | SWD_CLK | EZP_CLK | UART0_CTS | UART0_COL | FTM0_CH5
| | | | TPM1_CH1 | I2S0_TX_FS GND

GND
GND

AREF
VREFH

LCD_P36

LLWU_P8 | SPI0_PCS0 | UART1_TX | FTM0_CH3 | FB_AD11 | CMP1_OUT
| LCD_P42 | SPI0_MOSI | UART2_RX | TPM0_CH2 | SPI0_MISO ADC0_DP0
| | | | | TPM0_CH4
LLWU_P12 | SPI0_PCS0 | UART2_RTS | FTM3_CH0 | FB_ALE | FB_CS1 | FB_TS
LLWU_P14 | LCD_P44 | SPI1_PCS0 | UART2_RX | TPM0_CH4

ADC0_DM0
TPM0_CH3
LLWU_P13 | SPI0_SOUT | UART2_RX | FTM3_CH2 | FB_AD4 | I2C0_SCL
LLWU_P15 | LCD_P46 | ADC0_SE7B | SPI1_MOSI | UART0_RX | SPI1_MISO

NC

NC

NC

SPI0_PCS0 | UART0_TX | I2S0_RX_BCLK | I2S0_TXD0
SPI0_SIN | UART2_TX | FTM3_CH3 | FB_AD3 | I2C0_SDA
LCD_P47 | SPI1_MISO | UART0_TX | SPI1_MOSI
| | | | ADC1_DP0

ADC1_DM0

ADC1_SE18

SPI0_SCK | UART0_RX | I2S0_RXD0
ADC0_SE5B | SPI0_SCK | UART2_CTS | FTM3_CH1 | FB_CS0
LCD_P45 | ADC0_SE6B | SPI1_SCK | UART2_TX | TPM0_CH5
| | SPI0_SCK | UART0_RX | I2S0_RXD0
SPI0_MISO | SPI0_MOSI | I2S0_MCLK
| LCD_P9 | SPI1_SCK
ADC0_SE18 | UART4_RX | I2C0_SDA | EWM_IN
LCD_P48 | SPI1_MISO | UART1_TX | RTC_CLKOUT | CMP0_OUT | I2C1_SDA ------
| ADC0_SE17 | UART4_TX | I2C0_SCL | EWM_OUT
LCD_P49 | SPI1_MOSI | UART1_RX | SPI1_MISO | I2C1_SCL

ADC0_DP1

ADC0_DM1

ADC1_DP1

ADC1_DM1

DAC0_OUT
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

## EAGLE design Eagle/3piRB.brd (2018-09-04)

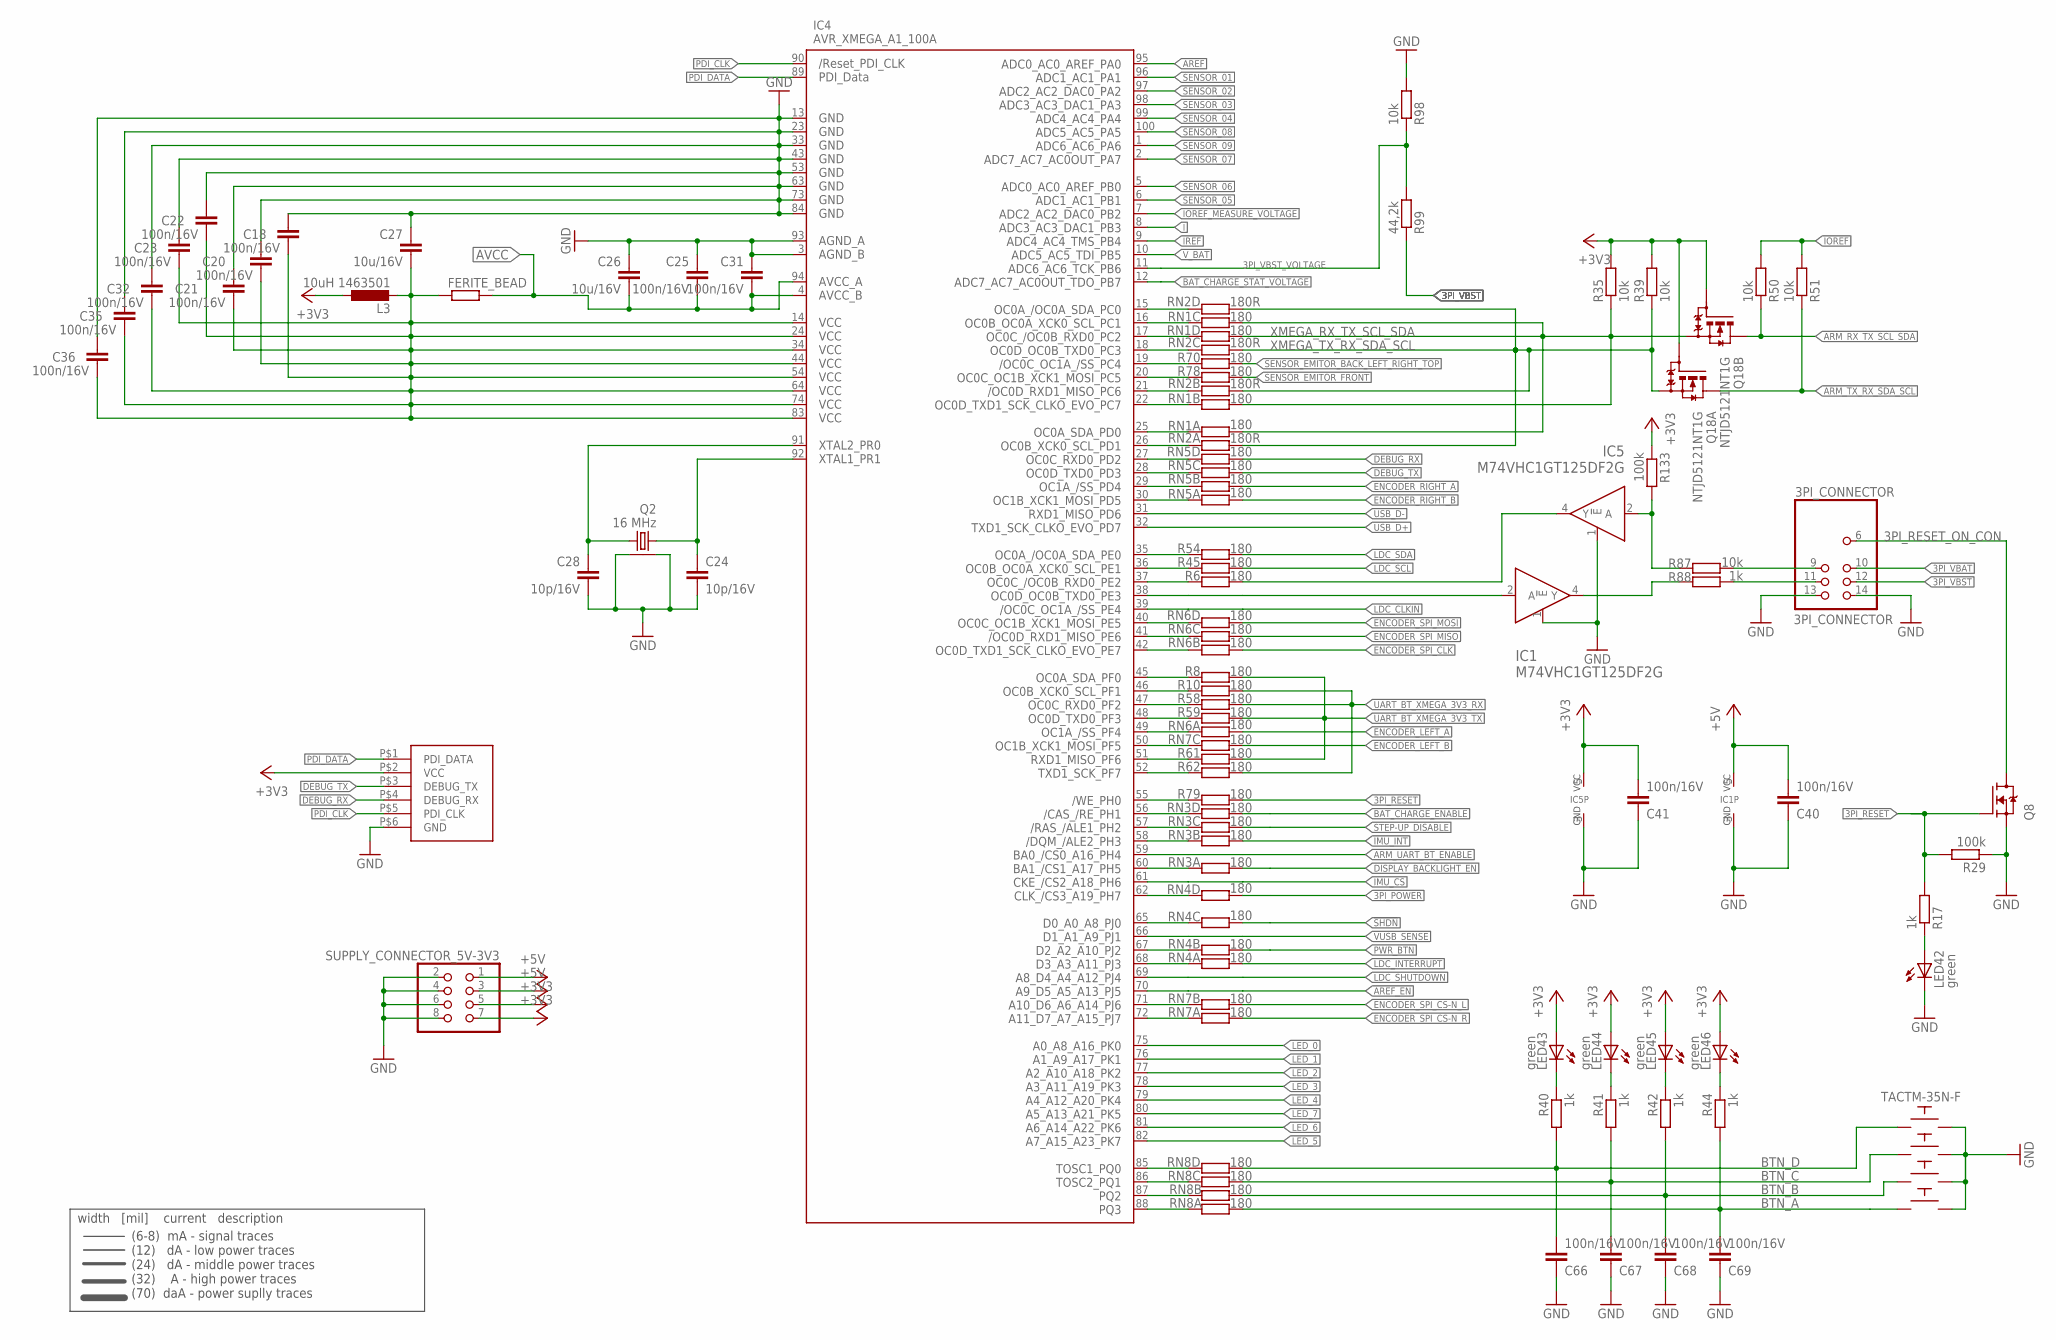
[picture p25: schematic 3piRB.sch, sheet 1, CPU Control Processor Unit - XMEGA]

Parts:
3PI_CONNECTOR: 3PI_CONNECTOR; 3PI_BT_CONNECTOR
BTN_A: TACTM-35N-F
BTN_B: TACTM-35N-F
BTN_C: TACTM-35N-F
BTN_D: TACTM-35N-F
C18, C20, C21, C22, C23, C25, C31, C32, C35, C36, C40, C41, C66, C67, C68, C69: 100n/16V; C0402
C24, C28: 10p/16V; C0603
C26, C27: 10u/16V; C0805
FERITE_BEAD: R-EU_R0603; R0603
IC1, IC5: M74VHC1GT125DF2G; SOT353
IC4: AVR_XMEGA_A1_100A; TQFP100
JP3: CON_PROG-6SMD; SMD-6
L3: 10uH 1463501; R0603
LED42, LED43, LED44, LED45, LED46: green; CHIPLED_0603
Q2: 16 MHz; ABM8
Q8: N-MOSFET-SOT323-GSD; SOT323
Q18: NTJD5121NT1G; SOT363
R6, R8, R10, R45, R54, R58, R59, R61, R62, R70, R78, R79: 180; _0402MP
R17, R40, R41, R42, R44, R88: 1k; _0402MP
R29, R133: 100k; _0402MP
R35, R39, R50, R51, R87, R98: 10k; _0402MP
R99: 44,2k; _0402MP
RN1, RN3, RN4, RN5, RN6, RN7, RN8: 180; 742-8
RN2: 180R; 742-8
SUPPLY_CONNECTOR_5V-3V3: PINHD-2X4; 2X04

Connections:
3PI-POWER: IC4.56 (PH1), RN3.4 (1)
3PI_POWER: RN4.5 (2); also elsewhere on the board
3PI_RESET: Q8.1 (G), R17.2, R29.2, R79.2
3PI_RESET_: IC4.55 (PH0), R79.1
3PI_RESET_ON_CON: 3PI_CONNECTOR.6, Q8.3 (D)
3PI_VBAT: 3PI_CONNECTOR.10; also elsewhere on the board
3PI_VBST: 3PI_CONNECTOR.12, R99.1; also elsewhere on the board
3PI_VBST_VOLTAGE: IC4.11 (PB6), R98.1, R99.2
3V3-L3-VCC_XMEGA: C18.2, C20.2, C21.2, C22.2, C23.2, C27.2, C32.2, C35.2, C36.2, FERITE_BEAD.2, IC4.14 (VCC1), IC4.24 (VCC2), IC4.34 (VCC3), IC4.44 (VCC4), IC4.54 (VCC5), IC4.64 (VCC6), IC4.74 (VCC7), IC4.83 (VCC8), L3.2
!SHDN: RN4.6 (2); also elsewhere on the board
+3V3: C41.2, IC5.5 (VCC), JP3.P$2 (VCC), L3.1, LED43.A, LED44.A, LED45.A, LED46.A, Q18.2 (G), Q18.5 (G), R35.2, R39.2, R133.1, SUPPLY_CONNECTOR_5V-3V3.5, SUPPLY_CONNECTOR_5V-3V3.7; also elsewhere on the board
+5V: C40.2, IC1.5 (VCC), SUPPLY_CONNECTOR_5V-3V3.1, SUPPLY_CONNECTOR_5V-3V3.3; also elsewhere on the board
AREF: IC4.95 (PA0); also elsewhere on the board
AREF_EN: IC4.70 (PJ5); also elsewhere on the board
ARM_RX_TX_SCL_SDA: Q18.3 (D), R50.1; also elsewhere on the board
ARM_TX_RX_SDA_SCL: Q18.6 (D), R51.1; also elsewhere on the board
ARM_UART_BT_ENABLE: IC4.59 (PH4); also elsewhere on the board
AVCC: C25.2, C26.2, C31.2, FERITE_BEAD.1, IC4.4 (AVCC_B), IC4.94 (AVCC_A); also elsewhere on the board
BAT_CHARGE_ENABLE: RN3.5 (2); also elsewhere on the board
BAT_CHARGE_ENABLE-A: IC4.62 (PH7), RN4.4 (1)
BAT_CHARGE_STAT_VOLTAGE: IC4.12 (PB7); also elsewhere on the board
BTN_A: BTN_A.P$2, C69.2, R44.2, RN8.8 (2)
BTN_A_: IC4.88 (PQ3), RN8.1
BTN_B: BTN_B.P$2, C68.2, R42.2, RN8.7 (2)
BTN_B_: IC4.87 (PQ2), RN8.2 (1)
BTN_C: BTN_C.P$2, C67.2, R41.2, RN8.6 (2)
BTN_C_: IC4.86 (PQ1), RN8.3 (1)
BTN_D: BTN_D.P$2, C66.2, R40.2, RN8.5 (2)
BTN_D_: IC4.85 (PQ0), RN8.4 (1)
DEBUG_RX: JP3.P$4 (DEBUG_RX), RN5.5 (2)
DEBUG_RX_: IC4.27 (PD2), RN5.4 (1)
DEBUG_TX: JP3.P$3 (DEBUG_TX), RN5.6 (2)
DEBUG_TX_: IC4.28 (PD3), RN5.3 (1)
DISPLAY_BACKLIGHT-EN: IC4.65 (PJ0), RN4.3 (1)
DISPLAY_BACKLIGHT_EN: RN3.8 (2); also elsewhere on the board
ENCODER_LEFT_A: RN6.8 (2); also elsewhere on the board
ENCODER_LEFT_A_: IC4.29 (PD4), RN5.2 (1)
ENCODER_LEFT_B: RN7.6 (2); also elsewhere on the board
ENCODER_LEFT_B_: IC4.30 (PD5), RN5.1
ENCODER_RIGHT_A: RN5.7 (2); also elsewhere on the board
ENCODER_RIGHT_A_: IC4.49 (PF4), RN6.1
ENCODER_RIGHT_B: RN5.8 (2); also elsewhere on the board
ENCODER_RIGHT_B_: IC4.50 (PF5), RN7.3 (1)
ENCODER_SPI_CLK: RN6.7 (2); also elsewhere on the board
ENCODER_SPI_CLK_: IC4.42 (PE7), RN6.2 (1)
ENCODER_SPI_CS-N_L: RN7.7 (2); also elsewhere on the board
ENCODER_SPI_CS-N_L_: IC4.71 (PJ6), RN7.2 (1)
ENCODER_SPI_CS-N_R: RN7.8 (2); also elsewhere on the board
ENCODER_SPI_CS-N_R_: IC4.72 (PJ7), RN7.1
ENCODER_SPI_MISO: RN6.6 (2); also elsewhere on the board
ENCODER_SPI_MISO_: IC4.41 (PE6), RN6.3 (1)
ENCODER_SPI_MOSI: RN6.5 (2); also elsewhere on the board
ENCODER_SPI_MOSI_: IC4.40 (PE5), RN6.4 (1)
GND: 3PI_CONNECTOR.13, 3PI_CONNECTOR.14, BTN_A.P$4, BTN_B.P$4, BTN_C.P$4, BTN_D.P$4, C18.1, C20.1, C21.1, C22.1, C23.1, C24.2, C25.1, C26.1, C27.1, C28.2, C31.1, C32.1, C35.1, C36.1, C40.1, C41.1, C66.1, C67.1, C68.1, C69.1, IC1.1 (!E), IC1.3 (GND), IC4.3 (AGND_B), IC4.13 (GND1), IC4.23 (GND2), IC4.33 (GND3), IC4.43 (GND4), IC4.53 (GND5), IC4.63 (GND6), IC4.73 (GND7), IC4.84 (GND8), IC4.93 (AGND_A), IC5.1 (!E), IC5.3 (GND), JP3.P$6 (GND), LED42.C, Q2.GND$1, Q2.GND$2, Q8.2 (S), R29.1, R98.2, SUPPLY_CONNECTOR_5V-3V3.2, SUPPLY_CONNECTOR_5V-3V3.4, SUPPLY_CONNECTOR_5V-3V3.6, SUPPLY_CONNECTOR_5V-3V3.8; also elsewhere on the board
I: IC4.8 (PB3); also elsewhere on the board
IMU-ENT: IC4.58 (PH3), RN3.2 (1)
IMU_CS: IC4.61 (PH6); also elsewhere on the board
IMU_INT: RN3.7 (2); also elsewhere on the board
IOREF: R50.2, R51.2; also elsewhere on the board
IOREF_MEASURE_VOLTAGE: IC4.7 (PB2); also elsewhere on the board
IREF: IC4.9 (PB4); also elsewhere on the board
LDC_CLKIN: IC4.39 (PE4); also elsewhere on the board
LDC_INTERRUPT: RN4.8 (2); also elsewhere on the board
LDC_INTERRUPT_: IC4.68 (PJ3), RN4.1
LDC_SCL: R45.1; also elsewhere on the board
LDC_SCL_: IC4.36 (PE1), R45.2
LDC_SDA: R54.1; also elsewhere on the board
LDC_SDA_: IC4.35 (PE0), R54.2
LDC_SHUTDOWN: IC4.69 (PJ4); also elsewhere on the board
LED_0: IC4.75 (PK0); also elsewhere on the board
LED_1: IC4.76 (PK1); also elsewhere on the board
LED_2: IC4.77 (PK2); also elsewhere on the board
LED_3: IC4.78 (PK3); also elsewhere on the board
LED_4: IC4.79 (PK4); also elsewhere on the board
LED_5: IC4.82 (PK7); also elsewhere on the board
LED_6: IC4.81 (PK6); also elsewhere on the board
LED_7: IC4.80 (PK5); also elsewhere on the board
LED_R_20: LED42.A, R17.1
unnamed: LED43.C, R40.1
unnamed: LED44.C, R41.1
unnamed: LED45.C, R42.1
unnamed: LED46.C, R44.1
PDI_CLK: IC4.90 (RESET), JP3.P$5 (PDI_CLK)
PDI_DATA: IC4.89 (PDI_DATA), JP3.P$1 (PDI_DATA)
PWR_BTN: RN4.7 (2); also elsewhere on the board
PWR_BTN_: IC4.57 (PH2), RN3.3 (1)
SENSOR_01: IC4.96 (PA1); also elsewhere on the board
SENSOR_02: IC4.97 (PA2); also elsewhere on the board
SENSOR_03: IC4.98 (PA3); also elsewhere on the board
SENSOR_04: IC4.99 (PA4); also elsewhere on the board
SENSOR_05: IC4.6 (PB1); also elsewhere on the board
SENSOR_06: IC4.5 (PB0); also elsewhere on the board
SENSOR_07: IC4.2 (PA7); also elsewhere on the board
SENSOR_08: IC4.100 (PA5); also elsewhere on the board
SENSOR_09: IC4.1 (PA6); also elsewhere on the board
SENSOR_EMITOR_BACK_LEFT_RIGHT_TOP: R70.2; also elsewhere on the board
SENSOR_EMITOR_BACK_LEFT_RIGHT_TOP_: IC4.20 (PC5), R78.1
SENSOR_EMITOR_FRONT: R78.2; also elsewhere on the board
SENSOR_EMITOR_FRONT_: IC4.19 (PC4), R70.1
SHDN_: IC4.67 (PJ2), RN4.2 (1)
STEP-UP_DISABLE: RN3.6 (2); also elsewhere on the board
STEP-UP_DISABLE_: IC4.60 (PH5), RN3.1
UART_3V3_3PI_RX: IC5.4 (Y), R6.2
UART_3V3_3PI_RX_: IC4.37 (PE2), R6.1
UART_3V3_3PI_TX: IC1.2 (A), IC4.38 (PE3)
UART_5V_3PI_RX: IC5.2 (A), R87.1, R133.2
UART_5V_3PI_RX_J: 3PI_CONNECTOR.9, R87.2
UART_5V_3PI_TX: IC1.4 (Y), R88.1
UART_5V_3PI_TX_J: 3PI_CONNECTOR.11, R88.2
UART_BT_XMEGA_3V3_RX: R10.2, R58.2, R62.2; also elsewhere on the board
UART_BT_XMEGA_3V3_RX_PF1-SCL: IC4.46 (PF1), R10.1
UART_BT_XMEGA_3V3_RX_PF2-RXD0: IC4.47 (PF2), R58.1
UART_BT_XMEGA_3V3_RX_PF7-TXD1: IC4.52 (PF7), R62.1
UART_BT_XMEGA_3V3_TX: R8.2, R59.2, R61.2; also elsewhere on the board
UART_BT_XMEGA_3V3_TX_PF0-SDA: IC4.45 (PF0), R8.1
UART_BT_XMEGA_3V3_TX_PF3-TXD0: IC4.48 (PF3), R59.1
UART_BT_XMEGA_3V3_TX_PF6-RXD1: IC4.51 (PF6), R61.1
USB_D+: IC4.32 (PD7); also elsewhere on the board
USB_D-: IC4.31 (PD6); also elsewhere on the board
VUSB_SENSE: IC4.66 (PJ1); also elsewhere on the board
V_BAT: IC4.10 (PB5); also elsewhere on the board
XMEGA_RX_TX_SCL_SDA: Q18.4 (S), R35.1, RN1.5 (2), RN1.6 (2), RN1.7 (2), RN1.8 (2)
XMEGA_RX_TX_SCL_SDA_PC1-SCL: IC4.16 (PC1), RN1.3 (1)
XMEGA_RX_TX_SCL_SDA_PC2-RXD0: IC4.17 (PC2), RN1.4 (1)
XMEGA_RX_TX_SCL_SDA_PC7-TXD1: IC4.22 (PC7), RN1.2 (1)
XMEGA_RX_TX_SCL_SDA_PD0-SDA: IC4.25 (PD0), RN1.1
XMEGA_TX_RX_SDA_SCL: Q18.1 (S), R39.1, RN2.5 (2), RN2.6 (2), RN2.7 (2), RN2.8 (2)
XMEGA_TX_RX_SDA_SCL_PC0-SDA: IC4.15 (PC0), RN2.4 (1)
XMEGA_TX_RX_SDA_SCL_PC3-TXD0: IC4.18 (PC3), RN2.3 (1)
XMEGA_TX_RX_SDA_SCL_PC6-RXD1: IC4.21 (PC6), RN2.2 (1)
XMEGA_TX_RX_SDA_SCL_PD1-SCL: IC4.26 (PD1), RN2.1
XTAL1: C24.1, IC4.92 (PR1), Q2.Q$1 (1)
XTAL2: C28.1, IC4.91 (PR0), Q2.Q$2 (2)

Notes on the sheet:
(6-8) mA - signal traces (12) dA - low power traces (24) dA - middle power traces (32) A - high power traces (70) daA - power suplly traces
width [mil] current description

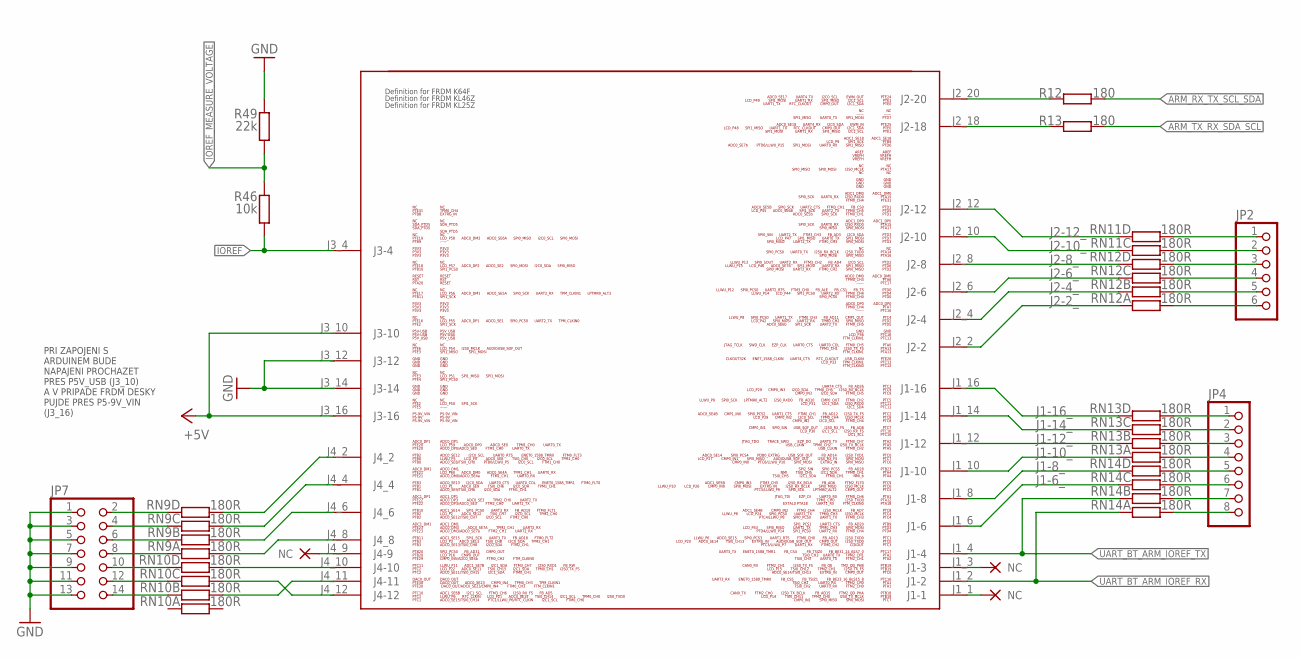
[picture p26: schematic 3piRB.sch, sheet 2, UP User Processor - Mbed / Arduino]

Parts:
JP2: PINHD-1X6; 1X06
JP4: PINHD-1X8; 1X08
JP7: PINHD-2X7; 2X07
R12, R13: 180; _0402MP
R46: 10k; _0402MP
R49: 22k; _0402MP
RN9, RN10, RN11, RN12, RN13, RN14: 180R; 742-8
U$1: FRDM-KL25Z+KL46Z+K64F_MORE_PINS

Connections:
+5V: U$1.J3_10 (J3-10), U$1.J3_16 (J3-16); also elsewhere on the board
ARM_RX_TX_SCL_SDA: R12.2; also elsewhere on the board
ARM_RX_TX_SCL_SDA_: R12.1, U$1.J2_20 (J2-20)
ARM_TX_RX_SDA_SCL: R13.2; also elsewhere on the board
ARM_TX_RX_SDA_SCL_: R13.1, U$1.J2_18 (J2-18)
GND: JP7.1, JP7.3, JP7.5, JP7.7, JP7.9, JP7.11, JP7.13, R49.2, U$1.J3_12 (J3-12), U$1.J3_14 (J3-14); also elsewhere on the board
IOREF: R46.1, U$1.J3_4 (J3-4); also elsewhere on the board
IOREF_MEASURE_VOLTAGE: R46.2, R49.1; also elsewhere on the board
J1-2: JP4.8, RN14.8 (2)
J1-4: JP4.7, RN14.7 (2)
J1-6: JP4.6, RN14.6 (2)
J1-6_: RN14.3 (1), U$1.J1_6 (J1-6)
J1-8: JP4.5, RN14.5 (2)
J1-8_: RN14.4 (1), U$1.J1_8 (J1-8)
J1-10: JP4.4, RN13.8 (2)
J1-10_: RN13.1, U$1.J1_10 (J1-10)
J1-12: JP4.3, RN13.7 (2)
J1-12_: RN13.2 (1), U$1.J1_12 (J1-12)
J1-14: JP4.2, RN13.6 (2)
J1-14_: RN13.3 (1), U$1.J1_14 (J1-14)
J1-16: JP4.1, RN13.5 (2)
J1-16_: RN13.4 (1), U$1.J1_16 (J1-16)
J2-2: JP2.6, RN12.8 (2)
J2-2_: RN12.1, U$1.J2_2 (J2-2)
J2-4: JP2.5, RN12.7 (2)
J2-4_: RN12.2 (1), U$1.J2_4 (J2-4)
J2-6: JP2.4, RN12.6 (2)
J2-6_: RN12.3 (1), U$1.J2_6 (J2-6)
J2-8: JP2.3, RN12.5 (2)
J2-8_: RN12.4 (1), U$1.J2_8 (J2-8)
J2-10: JP2.2, RN11.6 (2)
J2-10_: RN11.3 (1), U$1.J2_10 (J2-10)
J2-12: JP2.1, RN11.5 (2)
J2-12_: RN11.4 (1), U$1.J2_12 (J2-12)
J4-2: JP7.2, RN9.4 (1)
J4-2_: RN9.5 (2), U$1.J4_2
J4-4: JP7.4, RN9.3 (1)
J4-4_: RN9.6 (2), U$1.J4_4
J4-6: JP7.6, RN9.2 (1)
J4-6_: RN9.7 (2), U$1.J4_6
J4-8: JP7.8, RN9.1
J4-8_: RN9.8 (2), U$1.J4_8
J4-10: JP7.10, RN10.4 (1)
J4-10_: RN10.5 (2), U$1.J4_10 (J4-10)
J4-11: JP7.14, RN10.2 (1)
J4-11_: RN10.7 (2), U$1.J4_11 (J4-11)
J4-12: JP7.12, RN10.3 (1)
J4-12_: RN10.6 (2), U$1.J4_12 (J4-12)
UART_BT_ARM_IOREF_RX: RN14.1, U$1.J1_2 (J1-2); also elsewhere on the board
UART_BT_ARM_IOREF_TX: RN14.2 (1), U$1.J1_4 (J1-4); also elsewhere on the board

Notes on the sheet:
PRI ZAPOJENI S ARDUINEM BUDE NAPAJENI PROCHAZET PRES P5V_USB (J3_10) A V PRIPADE FRDM DESKY PUJDE PRES P5-9V_VIN (J3_16)

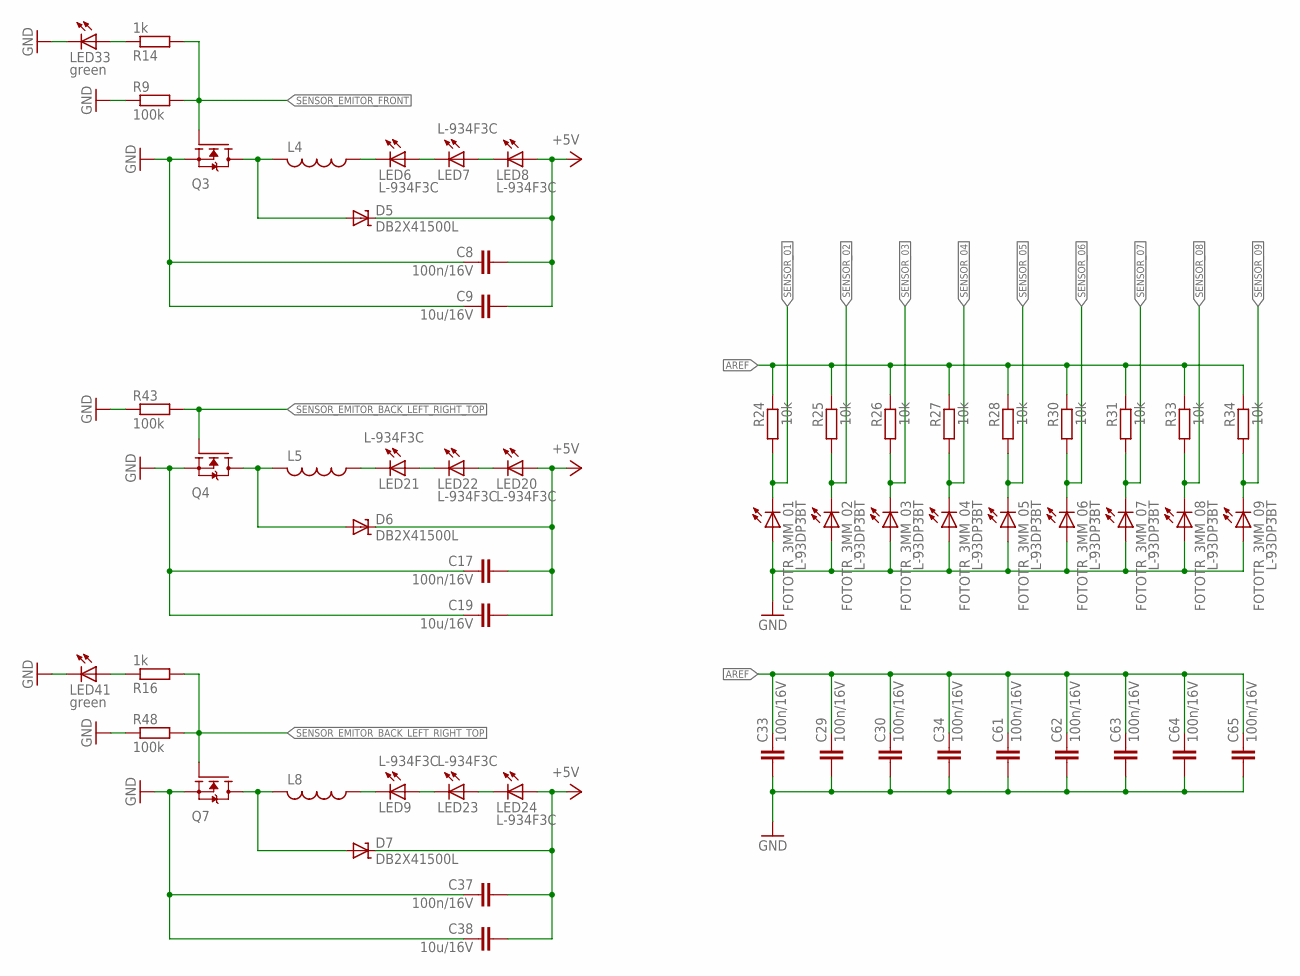
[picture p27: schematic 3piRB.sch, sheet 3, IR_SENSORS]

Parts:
C8, C17, C29, C30, C33, C34, C37, C61, C62, C63, C64, C65: 100n/16V; C0402
C9, C19, C38: 10u/16V; C0805
D5, D6, D7: DB2X41500L; SOD123
FOTOTR_3MM_01, FOTOTR_3MM_02, FOTOTR_3MM_03, FOTOTR_3MM_04, FOTOTR_3MM_05, FOTOTR_3MM_06, FOTOTR_3MM_07, FOTOTR_3MM_08, FOTOTR_3MM_09: L-93DP3BT; LED3MM
L4, L5, L8: L-USL0805; R0805@1
LED6, LED7, LED8, LED9, LED20, LED21, LED22, LED23, LED24: L-934F3C; LED3MM
LED33, LED41: green; CHIPLED_0603
Q3, Q4, Q7: N-MOSFET-SOT323-GSD; SOT323
R9, R43, R48: 100k; _0402MP
R14, R16: 1k; _0402MP
R24, R25, R26, R27, R28, R30, R31, R33, R34: 10k; _0402MP

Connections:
+5V: C8.1, C9.1, C17.1, C19.1, C37.1, C38.1, D5.C, D6.C, D7.C, LED8.A, LED20.A, LED24.A; also elsewhere on the board
AREF: C29.2, C30.2, C33.2, C34.2, C61.2, C62.2, C63.2, C64.2, C65.2, R24.1, R25.1, R26.1, R27.1, R28.1, R30.1, R31.1, R33.1, R34.1; also elsewhere on the board
GND: C8.2, C9.2, C17.2, C19.2, C29.1, C30.1, C33.1, C34.1, C37.2, C38.2, C61.1, C62.1, C63.1, C64.1, C65.1, FOTOTR_3MM_01.A, FOTOTR_3MM_02.A, FOTOTR_3MM_03.A, FOTOTR_3MM_04.A, FOTOTR_3MM_05.A, FOTOTR_3MM_06.A, FOTOTR_3MM_07.A, FOTOTR_3MM_08.A, FOTOTR_3MM_09.A, LED33.C, LED41.C, Q3.2 (S), Q4.2 (S), Q7.2 (S), R9.1, R43.1, R48.1; also elsewhere on the board
LED_R_8: LED33.A, R14.1
LED_R_19: LED41.A, R16.1
unnamed: LED20.K (C), LED22.A
unnamed: LED21.A, LED22.K (C)
unnamed: L5.1, LED21.K (C)
SENSOR_01: FOTOTR_3MM_01.K (C), R24.2; also elsewhere on the board
SENSOR_02: FOTOTR_3MM_02.K (C), R25.2; also elsewhere on the board
SENSOR_03: FOTOTR_3MM_03.K (C), R26.2; also elsewhere on the board
SENSOR_04: FOTOTR_3MM_04.K (C), R27.2; also elsewhere on the board
SENSOR_05: FOTOTR_3MM_05.K (C), R28.2; also elsewhere on the board
SENSOR_06: FOTOTR_3MM_06.K (C), R30.2; also elsewhere on the board
SENSOR_07: FOTOTR_3MM_07.K (C), R31.2; also elsewhere on the board
SENSOR_08: FOTOTR_3MM_08.K (C), R33.2; also elsewhere on the board
SENSOR_09: FOTOTR_3MM_09.K (C), R34.2; also elsewhere on the board
SENSOR_EMITORLEFT_RIGHT_TOP_COIL: D7.A, L8.2, Q7.3 (D)
SENSOR_EMITORLEFT_RIGHT_TOP_L0: L8.1, LED9.K (C)
SENSOR_EMITORLEFT_RIGHT_TOP_L1: LED9.A, LED23.K (C)
SENSOR_EMITORLEFT_RIGHT_TOP_L2: LED23.A, LED24.K (C)
SENSOR_EMITOR_BACK_COIL: D6.A, L5.2, Q4.3 (D)
SENSOR_EMITOR_BACK_LEFT_RIGHT_TOP: Q4.1 (G), Q7.1 (G), R16.2, R43.2, R48.2; also elsewhere on the board
SENSOR_EMITOR_FRONT: Q3.1 (G), R9.2, R14.2; also elsewhere on the board
SENSOR_EMITOR_FRONT_COIL: D5.A, L4.2, Q3.3 (D)
SENSOR_EMITOR_FRONT_L0: L4.1, LED6.K (C)
SENSOR_EMITOR_FRONT_L1: LED6.A, LED7.K (C)
SENSOR_EMITOR_FRONT_L2: LED7.A, LED8.K (C)

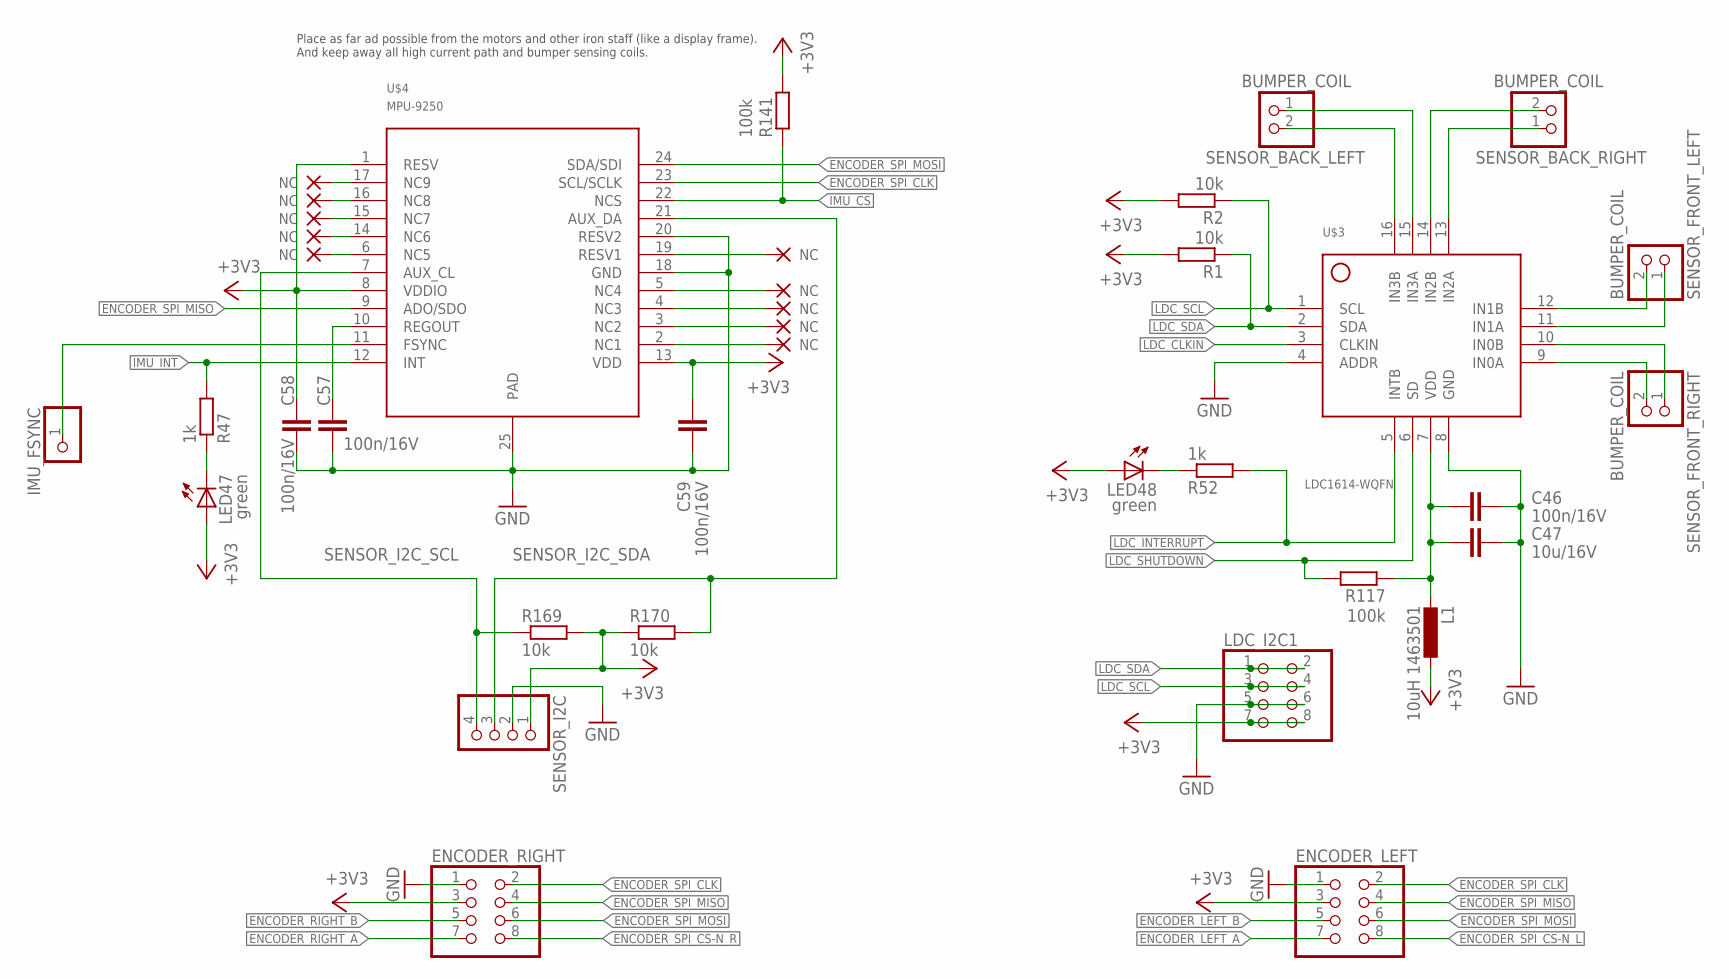
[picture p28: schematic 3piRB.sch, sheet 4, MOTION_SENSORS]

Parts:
C46, C57, C58, C59: 100n/16V; C0402
C47: 10u/16V; C0805
ENCODER_LEFT: PINHD-2X4; 2X04
ENCODER_RIGHT: PINHD-2X4; 2X04
IMU_FSYNC: PINHD-1X1; 1X01
L1: 10uH 1463501; R0603
LDC_I2C1: PINHD-2X4; 2X04
LED47, LED48: green; CHIPLED_0603
R1, R2, R169, R170: 10k; _0402MP
R47, R52: 1k; _0402MP
R117, R141: 100k; _0402MP
SENSOR_BACK_LEFT: BUMPER_COIL; 1X02
SENSOR_BACK_RIGHT: BUMPER_COIL; 1X02
SENSOR_FRONT_LEFT: BUMPER_COIL; 1X02
SENSOR_FRONT_RIGHT: BUMPER_COIL; 1X02
SENSOR_I2C: PINHD-1X4; 1X04
U$3: LDC1614-WQFN
U$4: MPU-9250; LEAD-QFN24

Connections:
+3V3: C58.1, C59.2, ENCODER_LEFT.3, ENCODER_RIGHT.3, L1.1, LDC_I2C1.7, LDC_I2C1.8, LED47.A, LED48.A, R1.2, R2.2, R141.2, R169.2, R170.1, SENSOR_I2C.1, U$4.1 (RESV), U$4.8 (VDDIO), U$4.13 (VDD); also elsewhere on the board
BUMPER_BACK_LEFT_A: SENSOR_BACK_LEFT.1, U$3.15 (IN3A)
BUMPER_BACK_LEFT_B: SENSOR_BACK_LEFT.2, U$3.16 (IN3B)
BUMPER_BACK_RIGHT_A: SENSOR_BACK_RIGHT.1, U$3.13 (IN2A)
BUMPER_BACK_RIGHT_B: SENSOR_BACK_RIGHT.2, U$3.14 (IN2B)
BUMPER_FRONT_LEFT_A: SENSOR_FRONT_LEFT.1, U$3.11 (IN1A)
BUMPER_FRONT_LEFT_B: SENSOR_FRONT_LEFT.2, U$3.12 (IN1B)
BUMPER_FRONT_RIGHT_A: SENSOR_FRONT_RIGHT.2, U$3.9 (IN0A)
BUMPER_FRONT_RIGHT_B: SENSOR_FRONT_RIGHT.1, U$3.10 (IN0B)
ENCODER_LEFT_A: ENCODER_LEFT.7; also elsewhere on the board
ENCODER_LEFT_B: ENCODER_LEFT.5; also elsewhere on the board
ENCODER_RIGHT_A: ENCODER_RIGHT.7; also elsewhere on the board
ENCODER_RIGHT_B: ENCODER_RIGHT.5; also elsewhere on the board
ENCODER_SPI_CLK: ENCODER_LEFT.2, ENCODER_RIGHT.2, U$4.23 (SCL/SCLK); also elsewhere on the board
ENCODER_SPI_CS-N_L: ENCODER_LEFT.8; also elsewhere on the board
ENCODER_SPI_CS-N_R: ENCODER_RIGHT.8; also elsewhere on the board
ENCODER_SPI_MISO: ENCODER_LEFT.4, ENCODER_RIGHT.4, U$4.9 (ADO/SDO); also elsewhere on the board
ENCODER_SPI_MOSI: ENCODER_LEFT.6, ENCODER_RIGHT.6, U$4.24 (SDA/SDI); also elsewhere on the board
GND: C46.2, C47.2, C57.1, C58.2, C59.1, ENCODER_LEFT.1, ENCODER_RIGHT.1, LDC_I2C1.5, LDC_I2C1.6, SENSOR_I2C.2, U$3.4 (ADDR), U$3.8 (GND), U$4.18 (GND), U$4.20 (RESV2), U$4.25 (PAD); also elsewhere on the board
IMU_CS: R141.1, U$4.22 (NCS); also elsewhere on the board
IMU_FSYNC: IMU_FSYNC.1, U$4.11 (FSYNC)
IMU_INT: R47.2, U$4.12 (INT); also elsewhere on the board
LDC_CLKIN: U$3.3 (CLKIN); also elsewhere on the board
LDC_INTERRUPT: R52.2, U$3.5 (INTB); also elsewhere on the board
LDC_PWR: C46.1, C47.1, L1.2, R117.1, U$3.7 (VDD)
LDC_SCL: LDC_I2C1.3, LDC_I2C1.4, R2.1, U$3.1 (SCL); also elsewhere on the board
LDC_SDA: LDC_I2C1.1, LDC_I2C1.2, R1.1, U$3.2 (SDA); also elsewhere on the board
LDC_SHUTDOWN: R117.2, U$3.6 (SD); also elsewhere on the board
unnamed: LED47.C, R47.1
unnamed: LED48.C, R52.1
NC_IMU_1: U$4.2 (NC1)
NC_IMU_2: U$4.3 (NC2)
NC_IMU_3: U$4.4 (NC3)
NC_IMU_4: U$4.5 (NC4)
NC_IMU_5: U$4.6 (NC5)
NC_IMU_6: U$4.14 (NC6)
NC_IMU_7: U$4.15 (NC7)
NC_IMU_8: U$4.16 (NC8)
NC_IMU_9: U$4.17 (NC9)
NC_IMU_RESV1: U$4.19 (RESV1)
REGOUT: C57.2, U$4.10 (REGOUT)
SENSOR_I2C_SCL: R169.1, SENSOR_I2C.4, U$4.7 (AUX_CL)
SENSOR_I2C_SDA: R170.2, SENSOR_I2C.3, U$4.21 (AUX_DA)

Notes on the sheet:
Place as far ad possible from the motors and other iron staff (like a display frame). And keep away all high current path and bumper sensing coils.

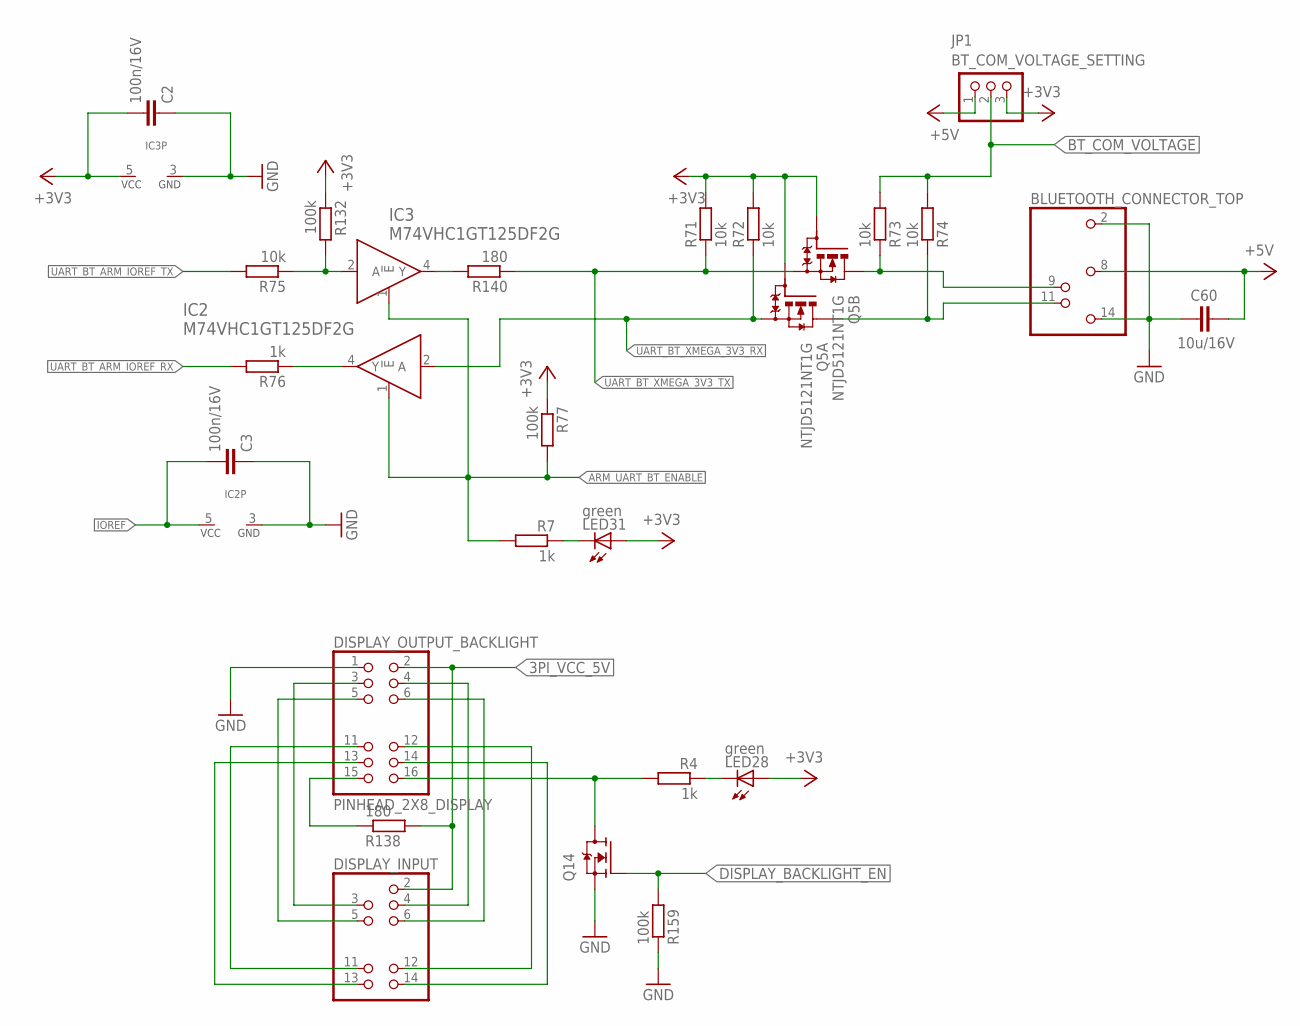
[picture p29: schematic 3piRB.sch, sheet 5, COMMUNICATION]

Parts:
BLUETOOTH_CONNECTOR_TOP: BLUETOOTH_CONNECTOR_TOP
C2, C3: 100n/16V; C0402
C60: 10u/16V; C0805
DISPLAY_INPUT: DISPLAY_INPUT
DISPLAY_OUTPUT_BACKLIGHT: PINHEAD_2X8_DISPLAY
IC2, IC3: M74VHC1GT125DF2G; SOT353
JP1: BT_COM_VOLTAGE_SETTING; 1X03
LED28, LED31: green; CHIPLED_0603
Q5: NTJD5121NT1G; SOT363
Q14: N-MOSFET-SOT323-GSD; SOT323
R4, R7, R76: 1k; _0402MP
R71, R72, R73, R74, R75: 10k; _0402MP
R77, R132, R159: 100k; _0402MP
R138, R140: 180; _0402MP

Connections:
3PI_VCC_5V: DISPLAY_INPUT.2, DISPLAY_OUTPUT_BACKLIGHT.2, R138.2; also elsewhere on the board
+3V3: C2.2, IC3.5 (VCC), JP1.3, LED28.A, LED31.A, Q5.2 (G), Q5.5 (G), R71.2, R72.2, R77.1, R132.1; also elsewhere on the board
+5V: BLUETOOTH_CONNECTOR_TOP.8, C60.2, JP1.1; also elsewhere on the board
ARM_UART_BT_ENABLE: IC2.1 (!E), IC3.1 (!E), R7.2, R77.2; also elsewhere on the board
BT_COM_VOLTAGE: JP1.2, R73.2, R74.2; also elsewhere on the board
DISPLAY_BACKLIGHT_EN: Q14.1 (G), R159.2; also elsewhere on the board
DISPLAY_BACKLIGHT_SW_GND: DISPLAY_OUTPUT_BACKLIGHT.16, Q14.3 (D), R4.2
DISPLAY_BACKLIGHT_VCC: DISPLAY_OUTPUT_BACKLIGHT.15, R138.1
DISPLAY_DB4: DISPLAY_INPUT.11, DISPLAY_OUTPUT_BACKLIGHT.11
DISPLAY_DB5: DISPLAY_INPUT.12, DISPLAY_OUTPUT_BACKLIGHT.12
DISPLAY_DB6: DISPLAY_INPUT.13, DISPLAY_OUTPUT_BACKLIGHT.13
DISPLAY_DB7: DISPLAY_INPUT.14, DISPLAY_OUTPUT_BACKLIGHT.14
DISPLAY_E: DISPLAY_INPUT.6, DISPLAY_OUTPUT_BACKLIGHT.6
DISPLAY_R!W: DISPLAY_INPUT.5, DISPLAY_OUTPUT_BACKLIGHT.5
DISPLAY_RS: DISPLAY_INPUT.4, DISPLAY_OUTPUT_BACKLIGHT.4
DISPLAY_V0: DISPLAY_INPUT.3, DISPLAY_OUTPUT_BACKLIGHT.3
GND: BLUETOOTH_CONNECTOR_TOP.2, BLUETOOTH_CONNECTOR_TOP.14, C2.1, C3.1, C60.1, DISPLAY_OUTPUT_BACKLIGHT.1, IC2.3 (GND), IC3.3 (GND), Q14.2 (S), R159.1; also elsewhere on the board
IOREF: C3.2, IC2.5 (VCC); also elsewhere on the board
unnamed: LED28.C, R4.1
unnamed: LED31.C, R7.1
UART_BT_5V_RX1: BLUETOOTH_CONNECTOR_TOP.11, Q5.6 (D), R74.1
UART_BT_5V_TX1: BLUETOOTH_CONNECTOR_TOP.9, Q5.3 (D), R73.1
UART_BT_ARM_IOREF-RX: IC2.4 (Y), R76.1
UART_BT_ARM_IOREF-TX: IC3.2 (A), R75.1, R132.2
UART_BT_ARM_IOREF_RX: R76.2; also elsewhere on the board
UART_BT_ARM_IOREF_TX: R75.2; also elsewhere on the board
UART_BT_XMEGA_3V3-TX: IC3.4 (Y), R140.2
UART_BT_XMEGA_3V3_RX: IC2.2 (A), Q5.1 (S), R72.1; also elsewhere on the board
UART_BT_XMEGA_3V3_TX: Q5.4 (S), R71.1, R140.1; also elsewhere on the board

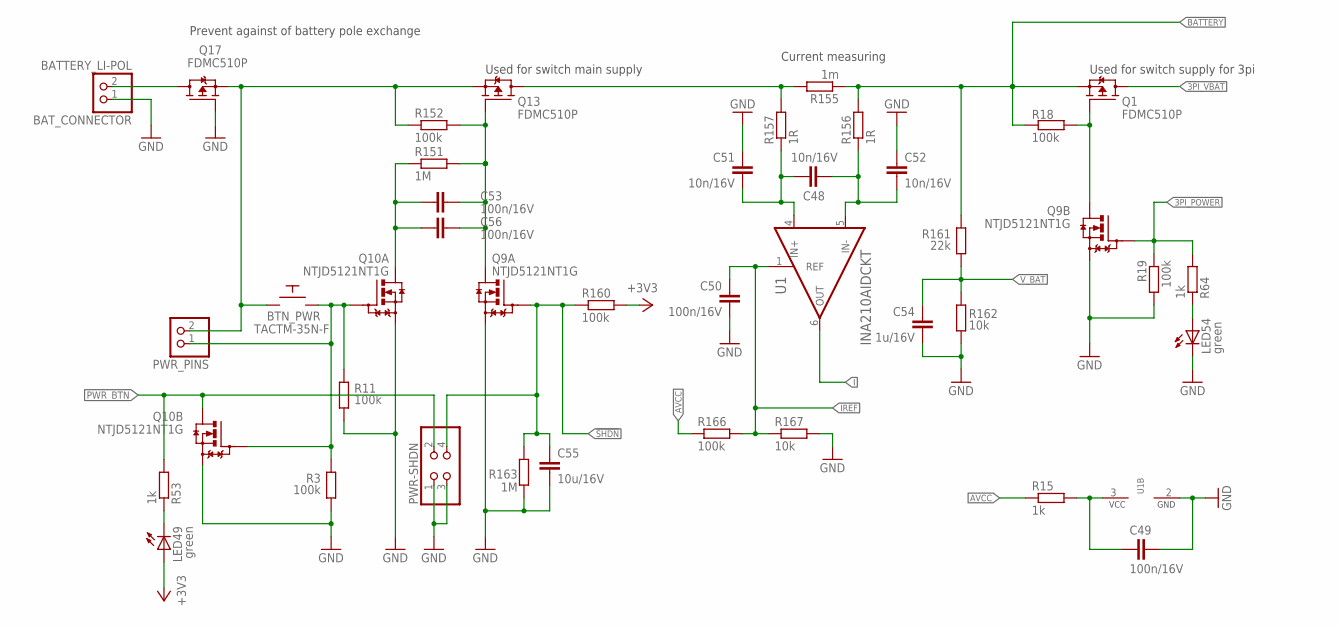
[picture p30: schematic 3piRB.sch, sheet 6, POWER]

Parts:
BAT_CONNECTOR: BATTERY_LI-POL; 1X02
BTN_PWR: TACTM-35N-F
C48, C51, C52: 10n/16V; C0402
C49, C50, C53, C56: 100n/16V; C0402
C54: 1u/16V; C0805
C55: 10u/16V; C0805
LED49, LED54: green; CHIPLED_0603
PWR-SHDN: PINHD-2X2; 2X02
PWR_PINS: PINHD-1X2; 1X02
Q1, Q13, Q17: FDMC510P; MLP3.3X3.3_HS
Q9, Q10: NTJD5121NT1G; SOT363
R3, R11, R18, R19, R152, R160, R166: 100k; _0402MP
R15, R53, R64: 1k; _0402MP
R151, R163: 1M; _0402MP
R155: 1m; 1206
R156, R157: 1R; _0402MP
R161: 22k; _0402MP
R162, R167: 10k; _0402MP
U1: INA210AIDCKT; SOT65P210X110-6N; MPN INA210AIDCKT

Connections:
3PI_POWER: Q9.5 (G), R19.1, R64.2; also elsewhere on the board
3PI_VBAT: Q1.5 (D), Q1.6 (D), Q1.7 (D), Q1.8 (D); also elsewhere on the board
3_PI_POWER_H_GATE: Q1.4 (G), Q9.3 (D), R18.2
!SHDN: C55.2, PWR-SHDN.4, Q9.2 (G), R160.1, R163.2; also elsewhere on the board
+3V3: LED49.A, R160.2; also elsewhere on the board
AVCC: R15.1, R166.1; also elsewhere on the board
BATTERY: Q1.1 (S), Q1.2 (S), Q1.3 (S), R18.1, R155.1, R156.2, R161.2; also elsewhere on the board
BATTERY_BEHIND_SWITCH: Q13.5 (D), Q13.6 (D), Q13.7 (D), Q13.8 (D), R155.2, R157.2
BATTERY_CONNECTOR: BAT_CONNECTOR.2, Q17.5 (D), Q17.6 (D), Q17.7 (D), Q17.8 (D)
BATTERY_REVERSE_PROTECTED: BTN_PWR.P$4, PWR_PINS.2, Q13.1 (S), Q13.2 (S), Q13.3 (S), Q17.1 (S), Q17.2 (S), Q17.3 (S), R152.2
BTN_PWR_: BTN_PWR.P$2, PWR_PINS.1, Q10.2 (G), Q10.5 (G), R3.2, R11.2
GND: BAT_CONNECTOR.1, C49.1, C50.1, C51.2, C52.2, C54.2, C55.1, LED54.C, PWR-SHDN.1, PWR-SHDN.3, Q9.1 (S), Q9.4 (S), Q10.1 (S), Q10.4 (S), Q17.4 (G), R3.1, R11.1, R19.2, R162.1, R163.1, R167.2, U1.2 (GND); also elsewhere on the board
I: U1.6 (OUT); also elsewhere on the board
IREF: C50.2, R166.2, R167.1, U1.1 (REF); also elsewhere on the board
I_AMP_PWR: C49.2, R15.2, U1.3 (VCC)
I_IN+: C48.1, C51.1, R157.1, U1.4 (IN+)
I_IN-: C48.2, C52.1, R156.1, U1.5 (IN-)
LED_R_25: LED54.A, R64.1
unnamed: LED49.C, R53.1
ON_SW: C53.2, C56.2, Q10.6 (D), R151.2
PWR_BTN: PWR-SHDN.2, Q10.3 (D), R53.2; also elsewhere on the board
SW_GATE: C53.1, C56.1, Q9.6 (D), Q13.4 (G), R151.1, R152.1
V_BAT: C54.1, R161.1, R162.2; also elsewhere on the board

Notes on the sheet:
Used for switch supply for 3pi
Prevent against of battery pole exchange
Used for switch main supply
Current measuring

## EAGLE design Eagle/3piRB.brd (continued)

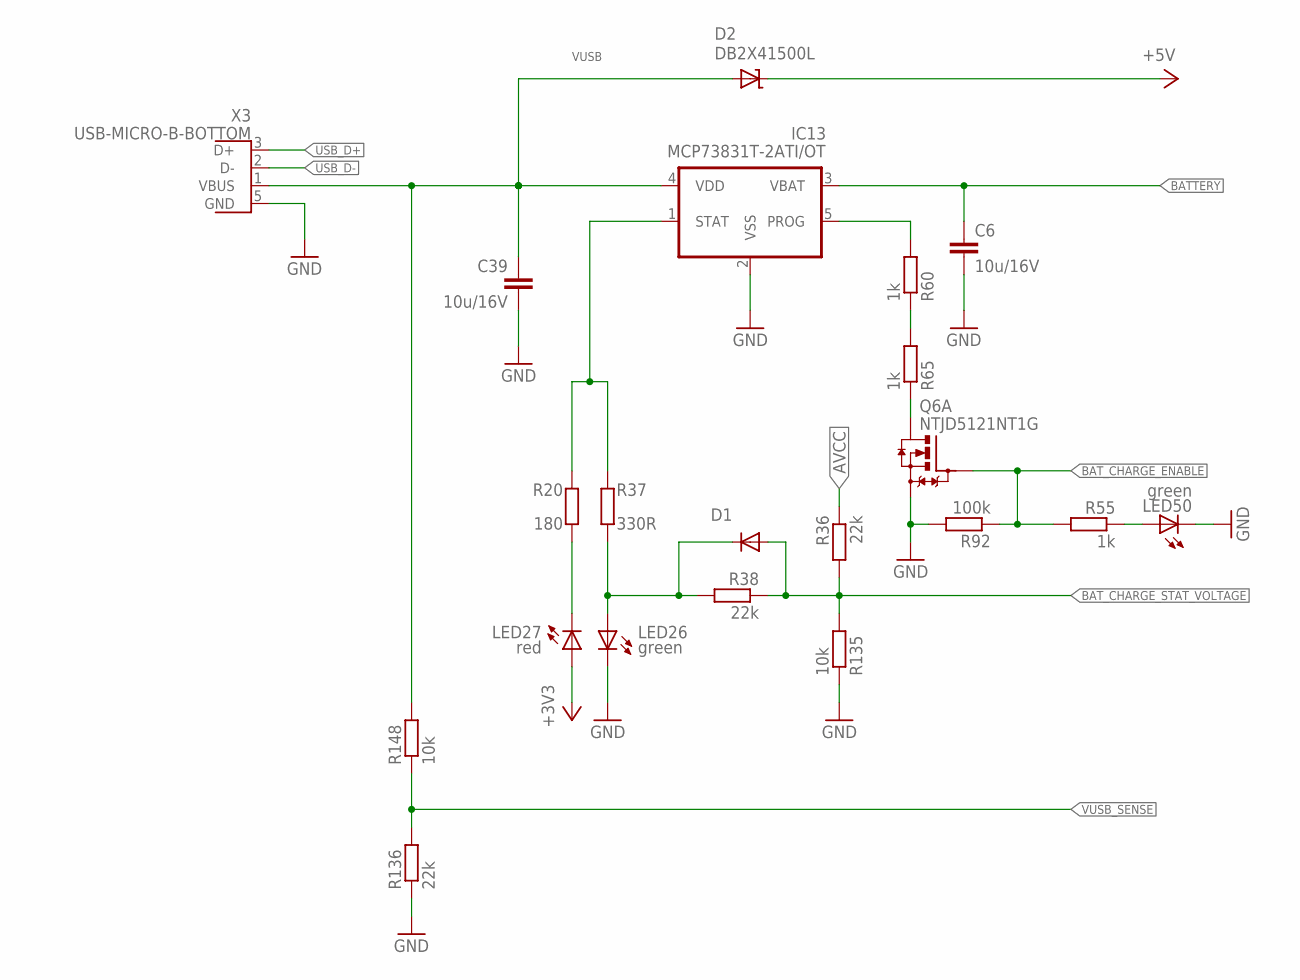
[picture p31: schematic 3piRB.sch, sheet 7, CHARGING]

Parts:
C6, C39: 10u/16V; C0805
D1: DIODE-0603; D0603
D2: DB2X41500L; SOD123
IC13: MCP73831T-2ATI/OT; SOT95P300X145-5N
LED26, LED50: green; CHIPLED_0603
LED27: red; CHIPLED_0603
Q6: NTJD5121NT1G; SOT363
R20: 180; _0402MP
R36, R38, R136: 22k; _0402MP
R37: 330R; _0402MP
R55, R60, R65: 1k; _0402MP
R92: 100k; _0402MP
R135, R148: 10k; _0402MP
X3: USB-MICRO-B-BOTTOM; USB-MICRO-B-BOTTOM-MOLEX

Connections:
+3V3: LED27.A; also elsewhere on the board
+5V: D2.C; also elsewhere on the board
AVCC: R36.1; also elsewhere on the board
BATTERY: C6.1, IC13.3 (VBAT); also elsewhere on the board
BAT_CHARGE_ENABLE: Q6.2 (G), R55.2, R92.1; also elsewhere on the board
BAT_CHARGE_STAT_VOLTAGE: D1.A, R36.2, R38.1, R135.2; also elsewhere on the board
GND: C6.2, C39.2, IC13.2 (VSS), LED26.C, LED50.C, Q6.1 (S), R92.2, R135.1, R136.1, X3.5 (GND); also elsewhere on the board
I_CHARGE_PROG-: IC13.5 (PROG), R60.2
LED_R_21: LED50.A, R55.1
unnamed: IC13.1 (STAT), R20.2, R37.2
unnamed: D1.C, LED26.A, R37.1, R38.2
unnamed: LED27.C, R20.1
unnamed: Q6.6 (D), R65.1
unnamed: R60.1, R65.2
USB_D+: X3.3 (D+); also elsewhere on the board
USB_D-: X3.2 (D-); also elsewhere on the board
VUSB: C39.1, D2.A, IC13.4 (VDD), R148.2, X3.1 (VBUS); also elsewhere on the board
VUSB_SENSE: R136.2, R148.1; also elsewhere on the board

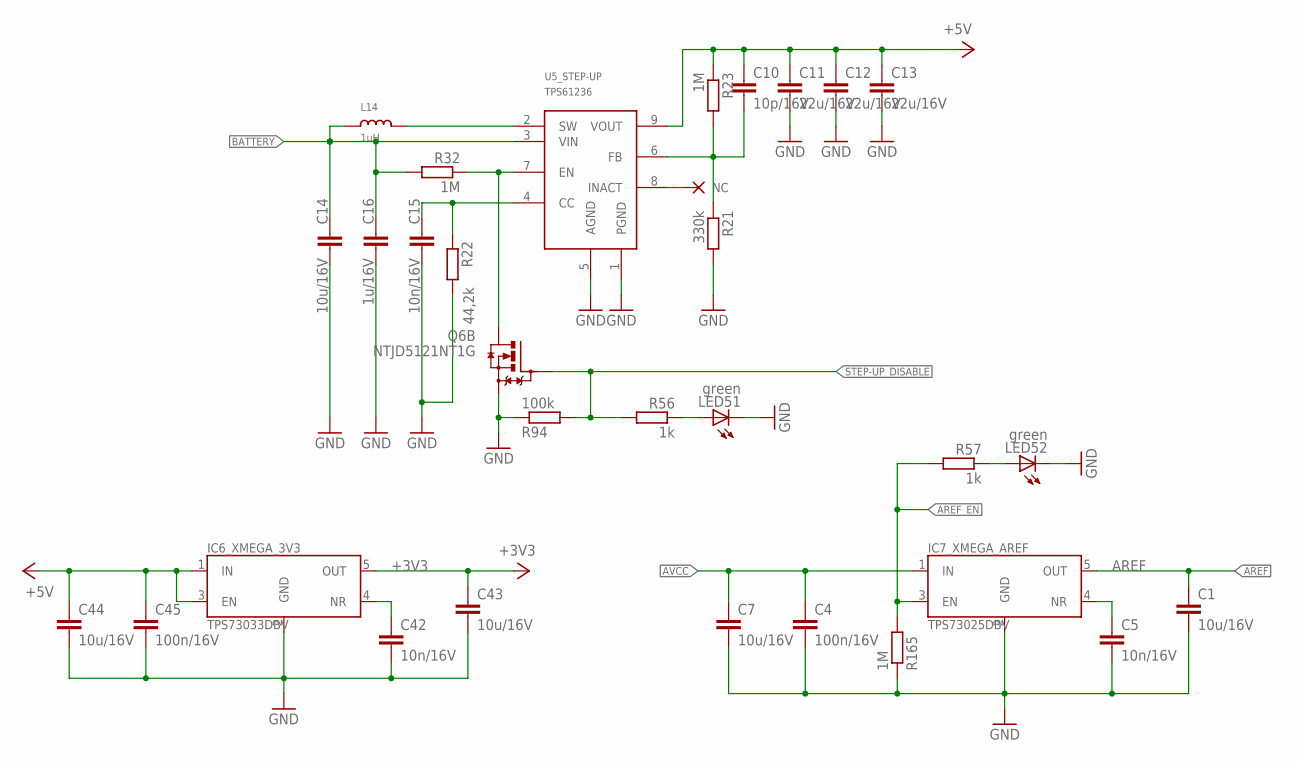
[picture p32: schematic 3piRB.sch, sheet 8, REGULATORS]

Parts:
C1, C7, C14, C43, C44: 10u/16V; C0805
C4, C45: 100n/16V; C0402
C5, C15, C42: 10n/16V; C0402
C10: 10p/16V; C0603
C11, C12, C13: 22u/16V; C0805; FARNELL 2611932
C16: 1u/16V; C0805
IC6_XMEGA_3V3: TPS73033DBV; SOT23-DBV
IC7_XMEGA_AREF: TPS73025DBV; SOT23-DBV
L14: 1uH; XAL7030
LED51, LED52: green; CHIPLED_0603
Q6: NTJD5121NT1G; SOT363
R21: 330k; _0402MP
R22: 44,2k; _0402MP
R23, R32, R165: 1M; _0402MP
R56, R57: 1k; _0402MP
R94: 100k; _0402MP
U5_STEP-UP: TPS61236; VQFN

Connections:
+3V3: C43.1, IC6_XMEGA_3V3.5 (OUT); also elsewhere on the board
+5V: C10.1, C11.1, C12.1, C13.1, C44.1, C45.1, IC6_XMEGA_3V3.1 (IN), IC6_XMEGA_3V3.3 (EN), R23.1, U5_STEP-UP.9 (VOUT); also elsewhere on the board
AREF: C1.1, IC7_XMEGA_AREF.5 (OUT); also elsewhere on the board
AREF_EN: IC7_XMEGA_AREF.3 (EN), R57.2, R165.2; also elsewhere on the board
AVCC: C4.1, C7.1, IC7_XMEGA_AREF.1 (IN); also elsewhere on the board
BATTERY: C14.1, C16.1, L14.1, R32.2, U5_STEP-UP.3 (VIN); also elsewhere on the board
GND: C1.2, C4.2, C5.2, C7.2, C11.2, C12.2, C13.2, C14.2, C15.2, C16.2, C42.2, C43.2, C44.2, C45.2, IC6_XMEGA_3V3.2 (GND), IC7_XMEGA_AREF.2 (GND), LED51.C, LED52.C, Q6.4 (S), R21.2, R22.2, R94.1, R165.1, U5_STEP-UP.1 (PGND), U5_STEP-UP.5 (AGND); also elsewhere on the board
LED_R_22: LED51.A, R56.1
LED_R_23: LED52.A, R57.1
NC_STEP-UP_INACT: U5_STEP-UP.8 (INACT)
STAB_2V5_NR: C5.1, IC7_XMEGA_AREF.4 (NR)
STAB_3V3_NR: C42.1, IC6_XMEGA_3V3.4 (NR)
STEP-UP_DISABLE: Q6.5 (G), R56.2, R94.2; also elsewhere on the board
STEP-UP_ENABLE: Q6.3 (D), R32.1, U5_STEP-UP.7 (EN)
STEP_UP_CC: C15.1, R22.1, U5_STEP-UP.4 (CC)
STEP_UP_FB: C10.2, R21.1, R23.2, U5_STEP-UP.6 (FB)
STEP_UP_SW: L14.2, U5_STEP-UP.2 (SW)

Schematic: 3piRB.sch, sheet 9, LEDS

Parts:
LED1, LED3, LED5, LED11, LED13, LED15, LED17, LED19: red; CHIPLED_0603
LED2, LED4, LED10, LED12, LED14, LED16, LED18, LED25, LED29, LED30, LED32, LED34, LED35, LED36, LED37, LED38, LED39, LED53: green; CHIPLED_0603
R5, R63, R139, R142, R143, R144, R145, R146, R147, R154: 1k; _0402MP
R100, R118, R120, R122, R124, R126, R128, R130: 150; _0402MP
R108, R119, R121, R123, R125, R127, R129, R131: 180; _0402MP

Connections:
3PI_VBAT: R63.2; also elsewhere on the board
3PI_VBST: R144.2; also elsewhere on the board
3PI_VCC_5V: R146.2; also elsewhere on the board
+3V3: LED1.A, LED3.A, LED5.A, LED11.A, LED13.A, LED15.A, LED17.A, LED19.A, R143.2; also elsewhere on the board
+5V: R139.2; also elsewhere on the board
AREF: R145.2; also elsewhere on the board
BATTERY: R154.2; also elsewhere on the board
BT_COM_VOLTAGE: R5.2; also elsewhere on the board
GND: LED2.C, LED4.C, LED10.C, LED12.C, LED14.C, LED16.C, LED18.C, LED25.C, LED29.C, LED30.C, LED32.C, LED34.C, LED35.C, LED36.C, LED37.C, LED38.C, LED39.C, LED53.C; also elsewhere on the board
IOREF: R147.2; also elsewhere on the board
LED_0: R100.2, R108.2; also elsewhere on the board
LED_1: R118.2, R119.2; also elsewhere on the board
LED_2: R120.2, R121.2; also elsewhere on the board
LED_3: R122.2, R123.2; also elsewhere on the board
LED_4: R124.2, R125.2; also elsewhere on the board
LED_5: R126.2, R127.2; also elsewhere on the board
LED_6: R128.2, R129.2; also elsewhere on the board
LED_7: R130.2, R131.2; also elsewhere on the board
LED_G_0: LED1.C, R108.1
LED_G_1: LED3.C, R119.1
LED_G_2: LED5.C, R121.1
LED_G_3: LED11.C, R123.1
LED_G_4: LED13.C, R125.1
LED_G_5: LED15.C, R127.1
LED_G_6: LED17.C, R129.1
LED_G_7: LED19.C, R131.1
LED_R_0: LED25.A, R100.1
LED_R_1: LED2.A, R118.1
LED_R_2: LED4.A, R120.1
LED_R_3: LED10.A, R122.1
LED_R_4: LED12.A, R124.1
LED_R_5: LED14.A, R126.1
LED_R_6: LED16.A, R128.1
LED_R_7: LED18.A, R130.1
LED_R_9: LED29.A, R5.1
LED_R_10: LED30.A, R154.1
LED_R_11: LED32.A, R139.1
LED_R_13: LED34.A, R142.1
LED_R_14: LED35.A, R143.1
LED_R_15: LED36.A, R144.1
LED_R_16: LED37.A, R145.1
LED_R_17: LED38.A, R146.1
LED_R_18: LED39.A, R147.1
LED_R_24: LED53.A, R63.1
VUSB: R142.2; also elsewhere on the board

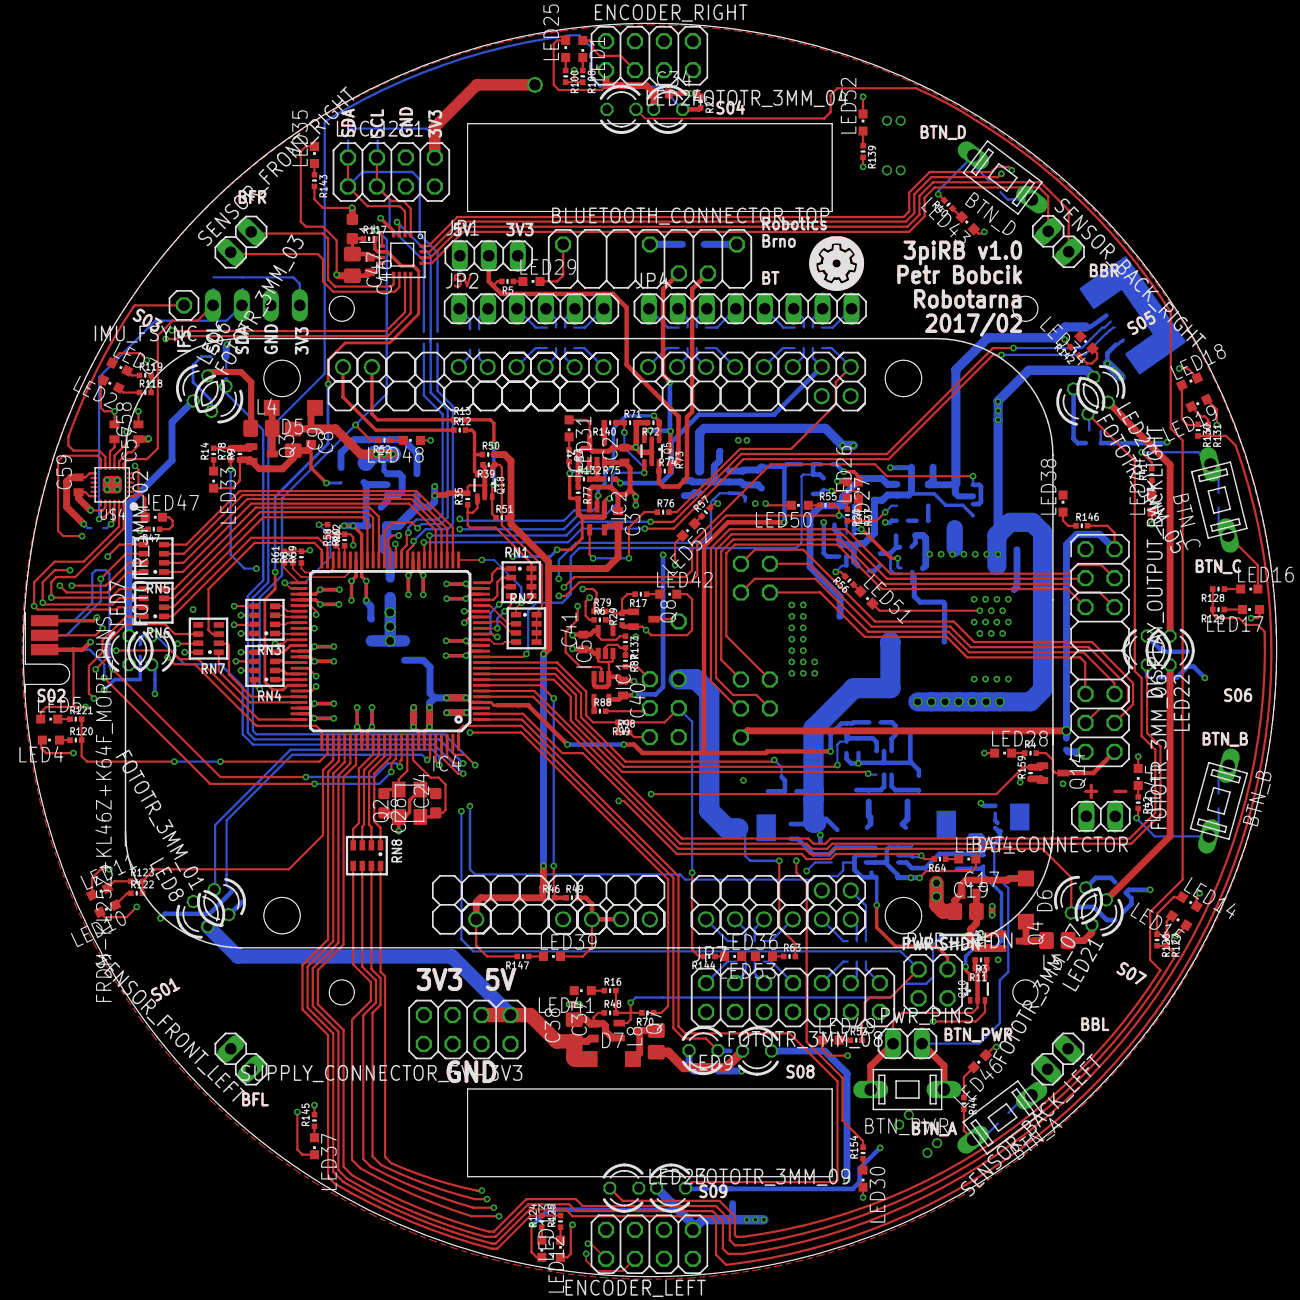
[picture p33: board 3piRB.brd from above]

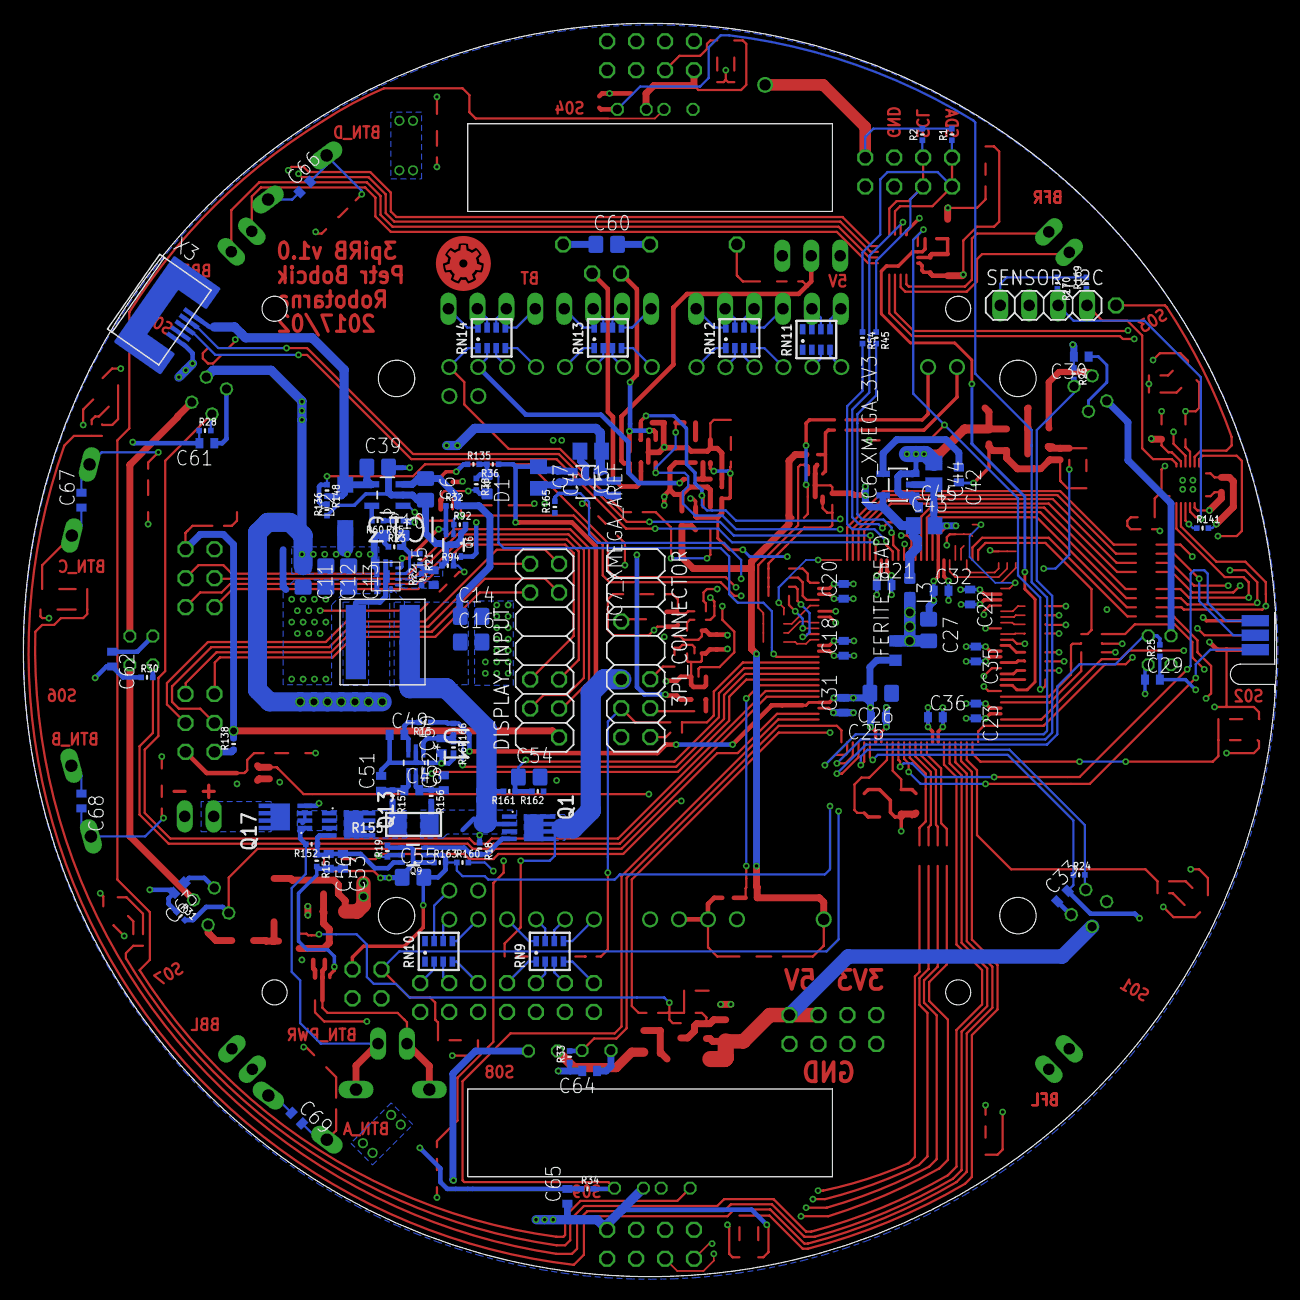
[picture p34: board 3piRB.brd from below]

Board: 4 copper layers, 110.0 x 110.0 mm, 341 parts (121 on the bottom side), 280 nets.

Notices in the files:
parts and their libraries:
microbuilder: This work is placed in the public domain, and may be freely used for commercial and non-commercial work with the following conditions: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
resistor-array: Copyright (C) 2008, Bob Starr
